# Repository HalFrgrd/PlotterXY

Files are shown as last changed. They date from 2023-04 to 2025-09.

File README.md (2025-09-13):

# PlotterXY

- Mainly based on https://github.com/jamescarruthers/PlotteRXY.
- I am using a different main board, y-axis, z-axis. Parts found in onshape.

## How to use
- Open fluidnc in the browser. See https://github.com/HalFrgrd/PlotterXY/blob/main/Firmware/readme.md
- Home all the axes.
- Generate some gcode using vpype. See https://github.com/HalFrgrd/PlotterXY/blob/main/Software/readme.md
- Upload or copy it over to the sd card.
- Plot!

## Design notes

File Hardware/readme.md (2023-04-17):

*The 2040 Y-axis is depreciated at this time.* Only print one Y-axis folder - depending on what extrusion profile you are using for your y-axis. Unless you are making a giant A0 or larger plotter then use the 2020 sized version. Note that this design hasn't been tested above A1 size.

# How long should my extrusions be?

Let's say you want to build an A2 machine; 600 x 420 (rounded up)

X extrusion = width + 240 = 600 + 240 = 840mm

Y extrusion = length + 180 = 420 + 180 = 600mm

Y axis = Y extrusion - 13 = 587mm

These numbers have a bit of excess to allow a bit of movement around the outside of the plot area.

A4: 
X: 297 + 240 = 537
Y: 210 + 180 = 390
Y moving axis: 390-13=377

A3: 
X: 420 + 240 = 660
Y: 297 + 180 = 477
Y moving axis: 477-13=464

Naming diagram

# Hardware build guide

1. Print out a corner pulley mount and check that it fits snuggly into your v-slot extrusion. If it doesn't you might need to recalibrate your printer.
2. Print out all the parts. The number at the end of the filename is the quantity you'll need — so Pulley_2.3mf means you need 2.
3. Layout out the extrusion and printed parts on a table according to the diagram above, work out where you will need to insert t-nuts. This is important because once you start assembly certain t-nuts are impossible to insert without loosening and/or disassembling.
4. Build up the z-axis gantry and slide it on to the y-axis.
5. Build up the y-axis carriages and attach them to the y-axis extrusion. All pulleys sit on a single shim and have two shims between the F605 bearings. Keep the screws that hold it to the y-axis loose for now.
6. Install the end caps and servo mounts to the extusions so you have an open sided C shape. Note the orientation of the servo mounts, they are opposite ways up with the flat part in the middle of the extrusion.
7. Slide the whole y-axis assembly on to the extrusion.
8. Install the pulley mounts, end caps and attach the final extrusion to close the frame.
9. Adjust all the mount screws until the frame is square. Adjust the eccentric nuts. The y-axis should slide left to right freely. Tighten the screws that hold the y-axis in place.
10. Install all the pulleys. They pulleys should sit on a single shim spacer, with two shims in between the two bearings.
11. Install the servos in to the servo mounts, being sure to vertically align the toothed pulley with the pulleys on the mount. Depending on the pulley you may need to use one of the stepper spacers between the motor and the mount to align the belt so that it sits in the middle of the teeth on the pulley.
12. Install belts and attach to the belt tension plate. They should not be tight at this stage — but should not droop. Leave at least 80mm of extra belt so that you can adjust it later.

Belt path
Belt path

13. Use the tensioners to get the belt tight. It should not be super tight, but the belt should not droop.
14. Attach the belt tension plate to the z-axis gantry.
15. Move the y-axis towards and up against the corner pulley mounts. Check that the y-axis is square by ensuring the gap between the rounded part of the y-axis carriages have equal space against the corner pulley mounts. Each y-axis carriage should sit flat against the corner pulleys. If they're not, then this means each belt has uneven tension. Use the belt tensioners to adjust, they should only need minimal movement.
16. Build up pen lift and install on to gantry.

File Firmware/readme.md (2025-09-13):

PlotterXY uses FluidNC: https://github.com/bdring/FluidNC

Using this main board: https://github.com/makerbase-mks/MKS-DLC32
- 12-24V input

Access FluidNC from a browser. VPN might cause problems.
- I changed it in the config to http://fluidncsmall.local/

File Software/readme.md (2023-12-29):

## vpype

Install vpype:
https://github.com/abey79/vpype

Install vpype-gcode
https://github.com/plottertools/vpype-gcode/

Use `vpype.toml`

Sample command (and good for calibrating position / scale):
`vpype --config vpype.toml rect 0cm 0cm 30cm 10cm linemerge --tolerance 0.1 linesimplify --tolerance 0.1 reloop --tolerance 0.1 linesort --two-opt layout --landscape a3 gwrite output.gcode`

- reloop: randomize seam location

## Useful projects
- https://anvaka.github.io/peak-map/#7.68/47.727/-122.574
- https://github.com/abey79/lines
- https://print.get-map.org
- https://wiki.openstreetmap.org/wiki/OSM_on_Paper

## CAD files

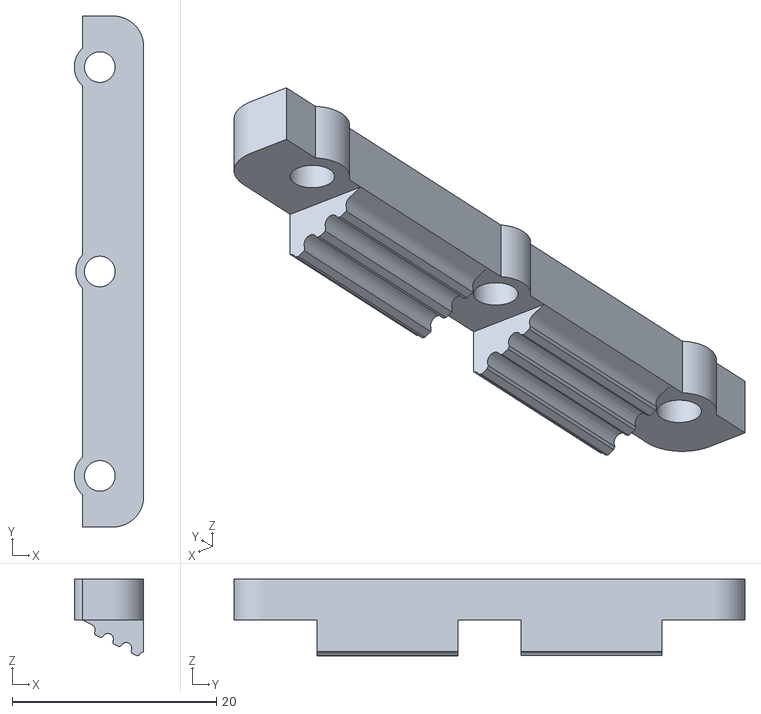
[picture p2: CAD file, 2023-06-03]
Hardware/Y-axis_2020/belt_clamp.stl
6.80 x 50.0 x 7.51

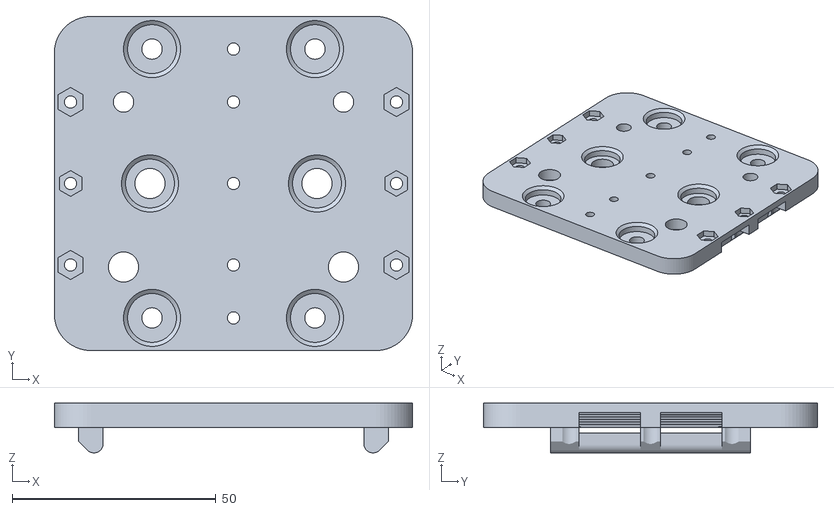
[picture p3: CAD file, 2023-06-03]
Hardware/Y-axis_2020/zaxis_gantry.stl
88.0 x 82.0 x 12.2

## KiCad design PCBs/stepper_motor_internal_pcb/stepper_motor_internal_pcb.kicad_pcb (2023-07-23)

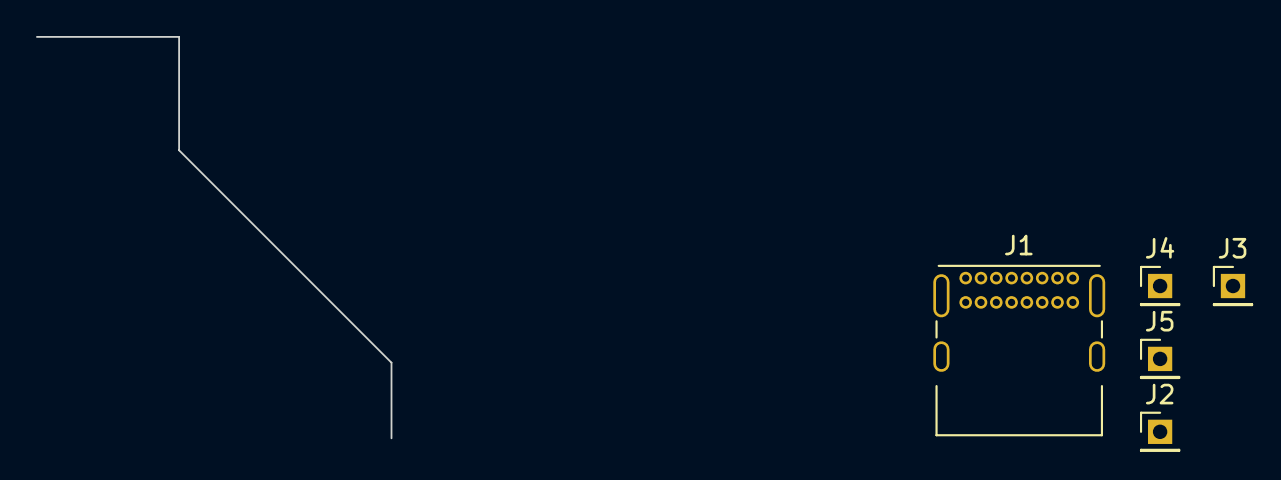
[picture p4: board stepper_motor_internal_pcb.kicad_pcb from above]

Board: 2 copper layers, 5 parts (0 on the bottom side), 2 nets, no tracks yet.

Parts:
J1: USB_C_Receptacle_USB2.0; USB_C_Receptacle_GCT_USB4085
J2, J3, J4, J5: Conn_01x01_Female; PinHeader_1x01_P2.00mm_Vertical

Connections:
unnamed: J1.A1 (GND), J1.A12 (GND), J1.B1 (GND), J1.B12 (GND)
unnamed: J1.A4 (VBUS), J1.A9 (VBUS), J1.B4 (VBUS), J1.B9 (VBUS)

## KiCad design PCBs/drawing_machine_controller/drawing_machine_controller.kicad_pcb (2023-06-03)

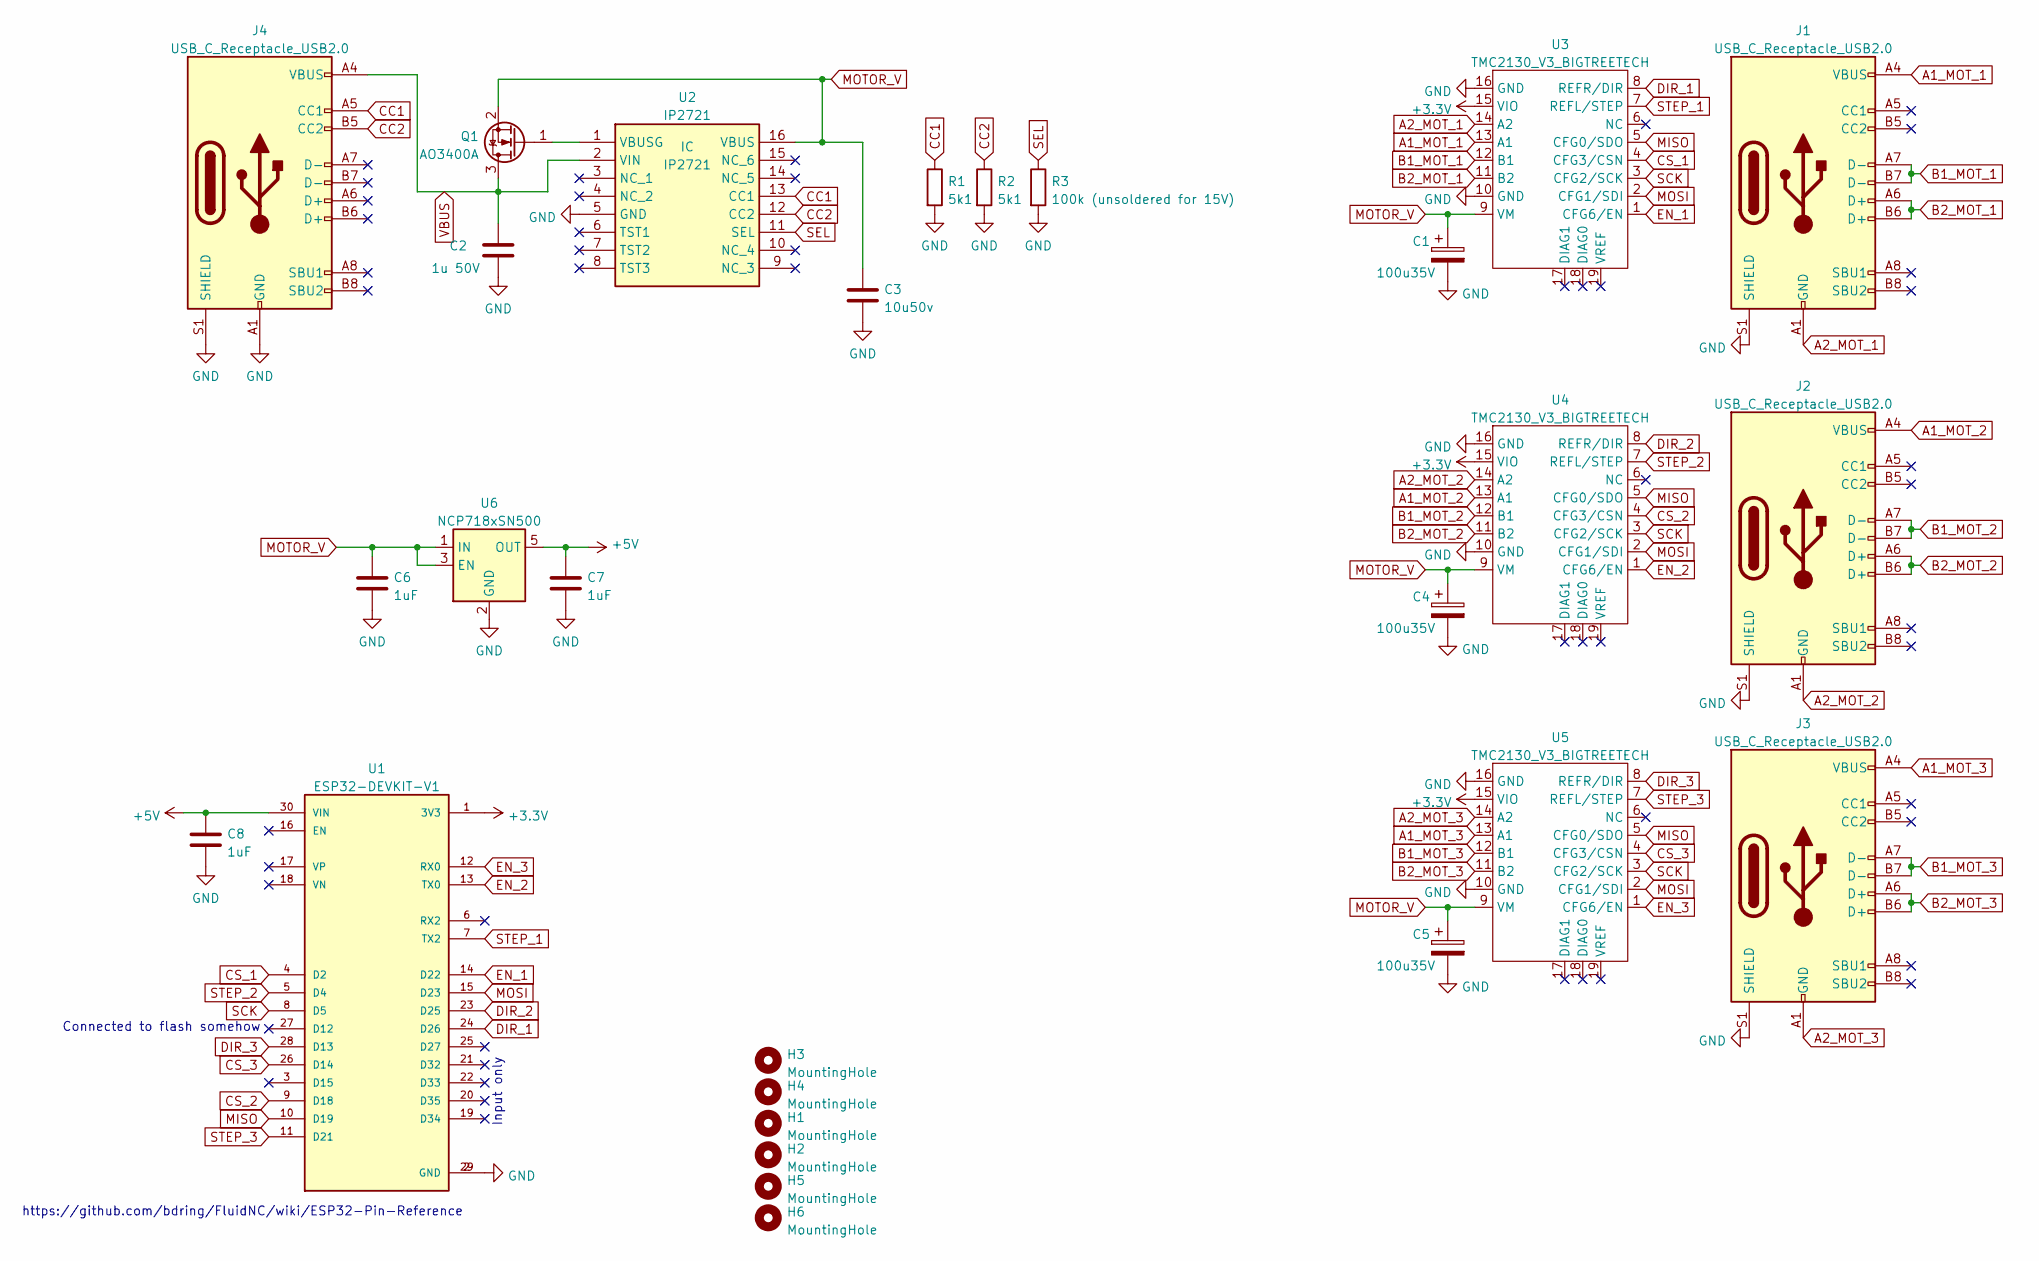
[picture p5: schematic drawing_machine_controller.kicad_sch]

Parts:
C1, C4, C5: 100u35V; CP_Elec_8x6.7
C2: 1u 50V; C_0805_2012Metric_Pad1.18x1.45mm_HandSolder
C3: 10u50v; C_0805_2012Metric_Pad1.18x1.45mm_HandSolder
C6, C7, C8: 1uF; C_0805_2012Metric_Pad1.18x1.45mm_HandSolder
H1, H2, H3, H4, H5, H6: MountingHole; MountingHole_5.3mm_M5_Pad_Via
J1, J2, J3, J4: USB_C_Receptacle_USB2.0; USB_C_Receptacle_GCT_USB4085
Q1: AO3400A; SOT-23
R1, R2: 5k1; R_0805_2012Metric_Pad1.20x1.40mm_HandSolder
R3: 100k (unsoldered for 15V); R_0805_2012Metric_Pad1.20x1.40mm_HandSolder
U1: ESP32-DEVKIT-V1; MODULE_ESP32_DEVKIT_V1; PARTREV N/A
U2: IP2721; SOP65P640X120-16N; Manufacturer_Part_Number IP2721
U3, U4, U5: TMC2130_V3_BIGTREETECH
U6: NCP718xSN500; SOT-23-5

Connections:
+3.3V: U1.1 (3V3), U3.15 (VIO), U4.15 (VIO), U5.15 (VIO)
+5V: C7.1, C8.2, U1.30 (VIN), U6.5 (OUT)
A1_MOT_1: J1.A4 (VBUS), J1.A9 (VBUS), J1.B4 (VBUS), J1.B9 (VBUS), U3.13 (A1)
A1_MOT_2: J2.A4 (VBUS), J2.A9 (VBUS), J2.B4 (VBUS), J2.B9 (VBUS), U4.13 (A1)
A1_MOT_3: J3.A4 (VBUS), J3.A9 (VBUS), J3.B4 (VBUS), J3.B9 (VBUS), U5.13 (A1)
A2_MOT_1: J1.A1 (GND), J1.A12 (GND), J1.B1 (GND), J1.B12 (GND), U3.14 (A2)
A2_MOT_2: J2.A1 (GND), J2.A12 (GND), J2.B1 (GND), J2.B12 (GND), U4.14 (A2)
A2_MOT_3: J3.A1 (GND), J3.A12 (GND), J3.B1 (GND), J3.B12 (GND), U5.14 (A2)
B1_MOT_1: J1.A7 (D-), J1.B7 (D-), U3.12 (B1)
B1_MOT_2: J2.A7 (D-), J2.B7 (D-), U4.12 (B1)
B1_MOT_3: J3.A7 (D-), J3.B7 (D-), U5.12 (B1)
B2_MOT_1: J1.A6 (D+), J1.B6 (D+), U3.11 (B2)
B2_MOT_2: J2.A6 (D+), J2.B6 (D+), U4.11 (B2)
B2_MOT_3: J3.A6 (D+), J3.B6 (D+), U5.11 (B2)
CC1: J4.A5 (CC1), R1.1, U2.13 (CC1)
CC2: J4.B5 (CC2), R2.1, U2.12 (CC2)
CS_1: U1.4 (D2), U3.4 (CFG3/CSN)
CS_2: U1.9 (D18), U4.4 (CFG3/CSN)
CS_3: U1.26 (D14), U5.4 (CFG3/CSN)
DIR_1: U1.24 (D26), U3.8 (REFR/DIR)
DIR_2: U1.23 (D25), U4.8 (REFR/DIR)
DIR_3: U1.28 (D13), U5.8 (REFR/DIR)
EN_1: U1.14 (D22), U3.1 (CFG6/EN)
EN_2: U1.13 (TX0), U4.1 (CFG6/EN)
EN_3: U1.12 (RX0), U5.1 (CFG6/EN)
GND: C1.2, C2.2, C3.2, C4.2, C5.2, C6.2, C7.2, C8.1, J1.S1 (SHIELD), J2.S1 (SHIELD), J3.S1 (SHIELD), J4.A1 (GND), J4.A12 (GND), J4.B1 (GND), J4.B12 (GND), J4.S1 (SHIELD), R1.2, R2.2, R3.2, U1.2 (GND), U1.29 (GND), U2.5 (GND), U3.10 (GND), U3.16 (GND), U4.10 (GND), U4.16 (GND), U5.10 (GND), U5.16 (GND), U6.2 (GND)
MISO: U1.10 (D19), U3.5 (CFG0/SDO), U4.5 (CFG0/SDO), U5.5 (CFG0/SDO)
MOSI: U1.15 (D23), U3.2 (CFG1/SDI), U4.2 (CFG1/SDI), U5.2 (CFG1/SDI)
MOTOR_V: C1.1, C3.1, C4.1, C5.1, C6.1, Q1.2 (S), U2.16 (VBUS), U3.9 (VM), U4.9 (VM), U5.9 (VM), U6.1 (IN), U6.3 (EN)
unnamed: Q1.1 (G), U2.1 (VBUSG)
SCK: U1.8 (D5), U3.3 (CFG2/SCK), U4.3 (CFG2/SCK), U5.3 (CFG2/SCK)
SEL: R3.1, U2.11 (SEL)
STEP_1: U1.7 (TX2), U3.7 (REFL/STEP)
STEP_2: U1.5 (D4), U4.7 (REFL/STEP)
STEP_3: U1.11 (D21), U5.7 (REFL/STEP)
VBUS: C2.1, J4.A4 (VBUS), J4.A9 (VBUS), J4.B4 (VBUS), J4.B9 (VBUS), Q1.3 (D), U2.2 (VIN)

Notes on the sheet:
https://github.com/bdring/FluidNC/wiki/ESP32-Pin-Reference
Connected to flash somehow
Input only

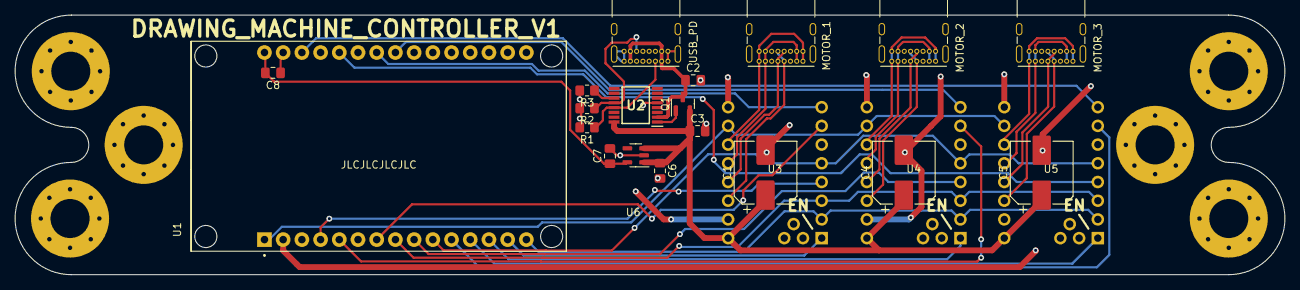
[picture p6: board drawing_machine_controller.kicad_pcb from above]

Board: 2 copper layers, 172.4 x 35.2 mm, 28 parts (0 on the bottom side), 36 nets.

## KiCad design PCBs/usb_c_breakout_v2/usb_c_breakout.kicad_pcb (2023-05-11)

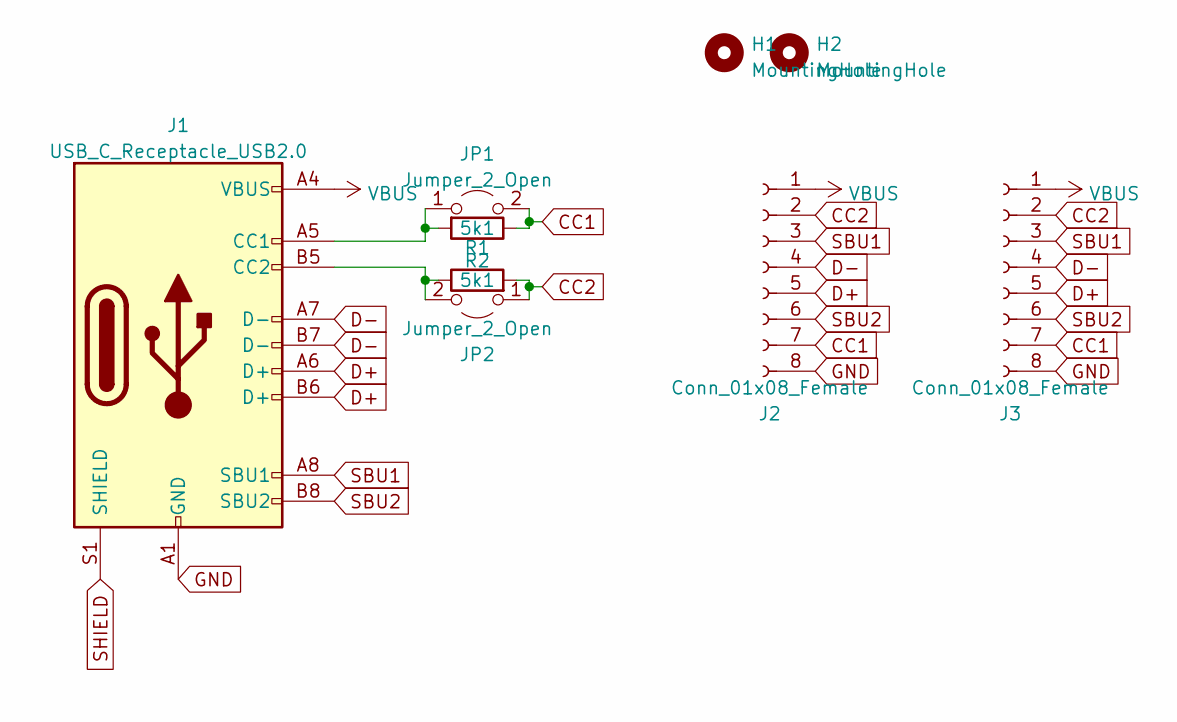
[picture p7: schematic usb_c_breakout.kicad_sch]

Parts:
H1, H2: MountingHole; MountingHole_3.2mm_M3_Pad_Via
J1: USB_C_Receptacle_USB2.0; USB_C_Receptacle_GCT_USB4085
J2, J3: Conn_01x08_Female; PinHeader_1x08_P2.54mm_Vertical
JP1, JP2: Jumper_2_Open; SolderJumper-2_P1.3mm_Open_RoundedPad1.0x1.5mm
R1, R2: 5k1; R_0603_1608Metric_Pad0.98x0.95mm_HandSolder

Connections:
CC1: J2.7, J3.7, JP1.2 (B), R1.1
CC2: J2.2, J3.2, JP2.1 (A), R2.2
D+: J1.A6 (D+), J1.B6 (D+), J2.5, J3.5
D-: J1.A7 (D-), J1.B7 (D-), J2.4, J3.4
GND: J1.A1 (GND), J1.A12 (GND), J1.B1 (GND), J1.B12 (GND), J2.8, J3.8
unnamed: J1.A5 (CC1), JP1.1 (A), R1.2
unnamed: J1.B5 (CC2), JP2.2 (B), R2.1
SBU1: J1.A8 (SBU1), J2.3, J3.3
SBU2: J1.B8 (SBU2), J2.6, J3.6
SHIELD: J1.S1 (SHIELD)
VBUS: J1.A4 (VBUS), J1.A9 (VBUS), J1.B4 (VBUS), J1.B9 (VBUS), J2.1, J3.1

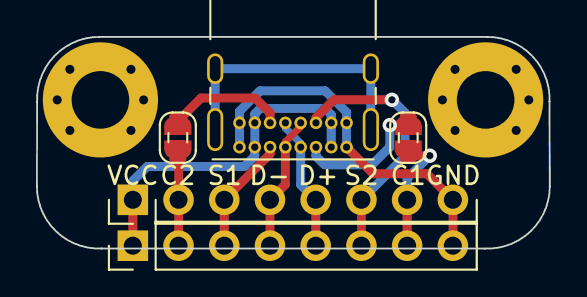
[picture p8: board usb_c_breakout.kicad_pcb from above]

Board: 2 copper layers, 28.5 x 11.8 mm, 9 parts (0 on the bottom side), 10 nets.

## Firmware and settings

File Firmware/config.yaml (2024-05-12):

board: MKS-DLC32
name: K40 MOD
meta: 2022-12-27 by Tong

Hostname: fluidncsmall

kinematics:
  corexy:

stepping:
  engine: I2S_STREAM
#Static only, Stream Produces a second "ghost line" when doing engraving/Filling
# 255 keeps motors neabled at all times
  idle_ms: 255
  pulse_us: 6
  dir_delay_us: 10
  disable_delay_us: 0

axes:
  shared_stepper_disable_pin: I2SO.0
  x:
    steps_per_mm: 80.000
    max_rate_mm_per_min: 4000.000
    acceleration_mm_per_sec2: 700.000
    max_travel_mm: 445.000
    soft_limits: true
    homing:
      cycle: 2
      positive_direction: false
      mpos_mm: 0.000
      feed_mm_per_min: 300.000
      seek_mm_per_min: 1800.000
      settle_ms: 500
      seek_scaler: 1.100
      feed_scaler: 1.100

    motor0:
      limit_neg_pin: gpio.36:low
      hard_limits: true
      pulloff_mm: 3.000
      stepstick:
        step_pin: I2SO.1
        direction_pin: I2SO.2:low


  y:
    steps_per_mm: 80.000
    max_rate_mm_per_min: 4000.000
    acceleration_mm_per_sec2: 700.000
    max_travel_mm: 340.000
    soft_limits: true
    homing:
      cycle: 1
      positive_direction: false
      mpos_mm: 0.000
      feed_mm_per_min: 300.000
      seek_mm_per_min: 1800.000
      settle_ms: 500
      seek_scaler: 1.100
      feed_scaler: 1.100

    motor0:
      limit_neg_pin: gpio.35:low
      hard_limits: true
      pulloff_mm: 3.000
      stepstick:
        step_pin: I2SO.5
        direction_pin: I2SO.6:low

  z:
    steps_per_mm: 50.000
    max_rate_mm_per_min: 2000.000
    acceleration_mm_per_sec2: 2000.000
    max_travel_mm: 8.000
    soft_limits: true
    homing:
      cycle: 0
      positive_direction: true
      mpos_mm: 0.000
      feed_mm_per_min: 50.000
      seek_mm_per_min: 50.000
      settle_ms: 500
      seek_scaler: 1.100
      feed_scaler: 1.100

    motor0:
      limit_pos_pin: gpio.34:low
      hard_limits: true
      pulloff_mm: 1.000
      stepstick:
        step_pin: I2SO.3
        direction_pin: I2SO.4

i2so:
  bck_pin: gpio.16
  data_pin: gpio.21
  ws_pin: gpio.17

spi:
  miso_pin: gpio.12
  mosi_pin: gpio.13
  sck_pin: gpio.14

sdcard:
  cs_pin: gpio.15
  card_detect_pin: gpio.39

coolant:
  flood_pin: NO_PIN
  mist_pin: NO_PIN
  delay_ms: 0

probe:
  pin: NO_PIN

start:
  must_home: false

# 5,18,19,22,23,25,26,27,32,33,39,I2SO.7
# SDA 0 / SCL 4

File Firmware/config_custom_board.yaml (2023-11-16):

name: "HF Plotter"
board: "HF Plotter"
# Uses TMC2130
# Future version idea: could make the steppers have a shared enable pin

stepping:
  engine: RMT
  idle_ms: 255
  dir_delay_us: 1
  pulse_us: 2
  disable_delay_us: 0

kinematics:
  corexy:

axes:
  shared_stepper_disable_pin: NO_PIN
  x:
    steps_per_mm: 800
    max_rate_mm_per_min: 2000
    acceleration_mm_per_sec2: 25
    max_travel_mm: 1000
    soft_limits: false
    homing:
      cycle: 2
      positive_direction: false
      mpos_mm: 150.000
      feed_mm_per_min: 100.000
      seek_mm_per_min: 200.000
      settle_ms: 500
      seek_scaler: 1.100
      feed_scaler: 1.100
    
    motor0:
      limit_neg_pin: NO_PIN
      limit_pos_pin: NO_PIN
      limit_all_pin: NO_PIN
      hard_limits: false
      pulloff_mm: 1.000
      tmc_2130:
        disable_pin: gpio.22:high
        direction_pin: gpio.26
        step_pin: gpio.17
        cs_pin: gpio.2
        r_sense_ohms: 0.110
        run_amps: 0.250
        hold_amps: 0.250
        microsteps: 32
        stallguard: 0
        stallguard_debug: false
        run_mode: StealthChop
        homing_mode: StealthChop
        use_enable: true
        toff_disable: 3
        toff_stealthchop: 5
        toff_coolstep: 3
    motor1:
      null_motor:

  y:
    steps_per_mm: 800
    max_rate_mm_per_min: 2000
    acceleration_mm_per_sec2: 25
    max_travel_mm: 1000
    soft_limits: false
    homing:
      cycle: 2
      positive_direction: false
      mpos_mm: 150.000
      feed_mm_per_min: 100.000
      seek_mm_per_min: 200.000
      settle_ms: 500
      seek_scaler: 1.100
      feed_scaler: 1.100

    motor0:
      limit_neg_pin: NO_PIN
      limit_pos_pin: NO_PIN
      limit_all_pin: NO_PIN
      tmc_2130:
        disable_pin: gpio.1:high
        direction_pin: gpio.25
        step_pin: gpio.4
        cs_pin: gpio.18
        r_sense_ohms: 0.110
        run_amps: 0.250
        hold_amps: 0.250
        microsteps: 32
        stallguard: 0
        stallguard_debug: false
        run_mode: StealthChop
        homing_mode: StealthChop
        use_enable: false
        toff_disable: 1
        toff_stealthchop: 5
        toff_coolstep: 3

    motor1:
      null_motor:

  z:
    steps_per_mm: 800
    max_rate_mm_per_min: 2000
    acceleration_mm_per_sec2: 25
    max_travel_mm: 1000
    soft_limits: false
    homing:
      cycle: 2
      positive_direction: false
      mpos_mm: 150.000
      feed_mm_per_min: 100.000
      seek_mm_per_min: 200.000
      settle_ms: 500
      seek_scaler: 1.100
      feed_scaler: 1.100

    motor0:
      limit_all_pin: NO_PIN
      tmc_2130:
        disable_pin: gpio.3:low
        direction_pin: gpio.13
        step_pin: gpio.21
        cs_pin: gpio.14
        r_sense_ohms: 0.110
        run_amps: 0.250
        hold_amps: 0.250
        microsteps: 32
        stallguard: 0
        stallguard_debug: false
        run_mode: StealthChop
        homing_mode: StealthChop
        use_enable: false
        
spi:
  miso_pin: gpio.19
  mosi_pin: gpio.23
  sck_pin: gpio.5

sdcard:
  cs_pin: NO_PIN
  card_detect_pin: NO_PIN

coolant:
  flood_pin: NO_PIN
  mist_pin:  NO_PIN

probe:
  pin: NO_PIN

start:
  must_home: false

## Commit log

2023-06-03 pcb tweak, fluidnc start
    [belt_clamp.stl, drawing_machine_controller.kicad_pcb, drawing_machine_controller.kicad_sch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]
2023-07-23 basic config
    [stepper_motor_internal_pcb.kicad_pcb, stepper_motor_internal_pcb.kicad_sch]
2023-11-16 new chinese board
    [drawing_machine_controller.kicad_sch]
2023-11-22 got homing working
